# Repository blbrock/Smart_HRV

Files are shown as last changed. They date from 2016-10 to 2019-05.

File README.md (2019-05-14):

# Smart HRV  
Smart HRV replaces OEM controllers for Carrier (and probably Venmar and other brand) Heat Recovery Ventilation  
units.  Smart HRV adds intelligence to system controls using indoor and outdoor sensors to montior humidity and  
to manage humidity, fresh air, and odor control optimal performance. Smart HRV also integrates with fan and dehumidifier  
controls on Nest thermostats.  The system consists of an arduino-based control unit, one or more indoor humidity sensors.  
An outdoor temperature and humidity sensor, and an android user interface app to provide monitoring and control of system   
functions.  
  
The current system is customized to our own application and will likely need modification for other applications. But the   
package includes basic serial control logic for controlling an HRV and hopefully can provide guidance for others wishing  
to improve permormance of their heat recovery ventialation systems.  
  
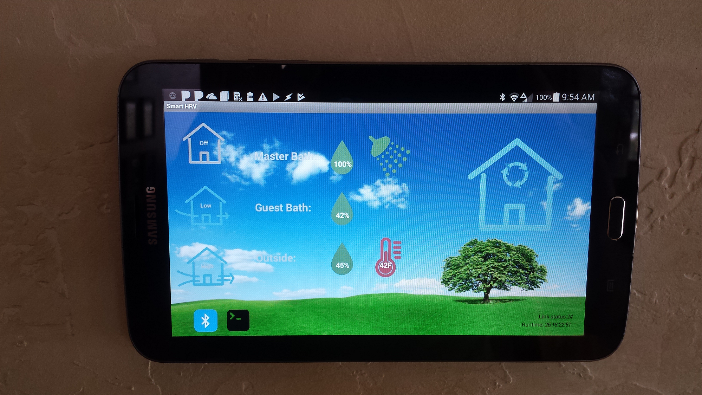
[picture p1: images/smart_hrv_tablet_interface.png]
Smart HRV Control Panel
  
  
# Background  
HRV and ERV (Energy Recovery Ventillator) have three basic functions:  
  
1. Manage indoor air quality efficiently by exchange fresh outdoor air for stale indoor air while recovering a portion of the heat from the exhaust airstream to conserve energy. 
 
2. Manage indoor humidity to reduce damage around windows and other cold surfaces by exchanging moist indoor air with dryer outdoor air; again recovering a portion of the heat from the exhaust air stream.  

3. Manage odors by exhausting indoor air.  
  
HRV/ERV systems work very well but the controls that came with ours (and most other units) fail on all three of their intended tasks.  Many units like ours lack any sort of timer circuit to allow fresh air exchange to be cycled. Instead, manufacturers and many HVAC expert claim the unit should be run continuously to maintain a steady flow of fresh air. This is insane! Heat recovery efficiency ranges from around 60%-70% for HRV units like ours, to about 90% for the newest ERV units. That means for every cubic foot of air exhausted by our unit, we lose 40% of the heat it contains. Heat we paid dearly to produce! Sure, it's better than opening a window but cycling the unit can provide plenty of fresh air while saving a significant amount of heat. Second, the best humidity to keep your house in winter depends on the outside temperature. The colder it is outside, the more likely moisture is to condense on windows so you need lower indoor humidity to prevent it. Also, the ability to reduce humidity by echanging indoor and outdoor air depends on the humidity outside. Luckily, outdoor humidity drops with the temperatue so on cold days, there is a good chance it is dryer outside than inside. But still, basic HRV units have no way to know if exchanging air will help and they could run in futility without reducing indoor humidity on wet days. Basic controllers have a manual dial setting to adjust the target indoor humidity. But outdoor temperatures fluctuate wildly over the day and season and nobody has the time to constantly fiddle with the dial to guess what the weather is going to do. This leads to settings that either run too little or too much so wind up with condensation damage on the windows anyway, wasted heat loss, or both. Finally, HRV/ERV units often include manual push buttons installed in bathrooms and laundry rooms that run for a set time when humidity or odor control is needed. OUrs ran for 20 minutes on a push which was not enough time to eliminate humidity after a shower, and certainly not enough time to eliminate odors when the relatives are visiting.

After years of frustration and some band-aid fixes for these inadequate controls, the catalyst to do something came when I purchased several Nest thermostats for our house and realized they provided fan and dehumidifier control functions that could improve the situation.  The fan control provided adjustable fresh air cycling and the dehumidifier provided the possibility of continuously monitoring outdoor temps and updating the humidity setpoint to always have the HRV trying to achieve the optimal humidity. I thought it would be just a matter of throwing in a couple of relays to get the Nest talking to the HRV but I was wrong.  There is no provision for such a setup so the only good option was to hack the controller.  So I set about reverse engineering the serial ttl communication logic, tossing out the old ugly wall controller and replacing it with an arduino controller interfaced with a cheap used android tablet mounted on the wall. The result is the Smart HRV system which has been chugging along with continuous tweaks for about two years now.

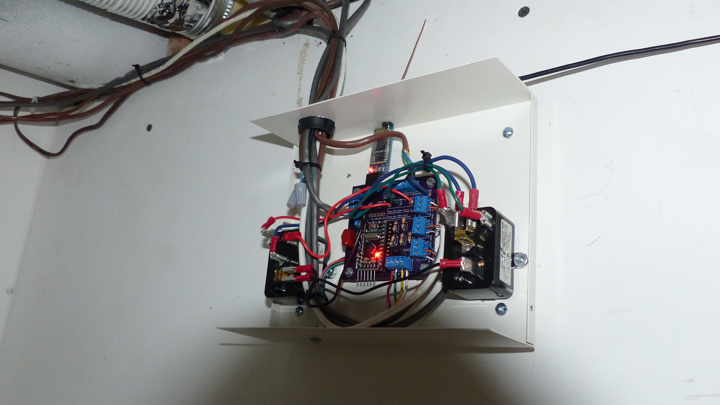
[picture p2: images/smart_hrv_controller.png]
Smart HRV Controller
  
  
# Features: 

1. Monitors indoor humidity in multiple rooms and outdoor temperature and humidity to automatically and intelligently determine optimal inddor humidity levels and initiate fresh air exchange or recirculation cycles to achieve target humidity with minimal heat loss.

2. Integrates with Nest thermostat to allow fan controls on thermostat to initiate low speed air exchange cycles.

3. Defrost indicator on user interface to show when a defrost recirculating cycle is active.

4. Tracks cumulative run time and alerts users when it is time to service filters.  

# Extras:  

# Error checking and logging:   

# Known Bugs:

- The HRV unit may enter an error condition if someone manually presses a ventilation button in a bathroom while an automated dehumidification cycle is already in progress.  This appears to be due to some internal control logic within the HRV.  My work around is to power cycle the HRV unit if that happens to reset the error condition.  A better solution would be to wire the manual ventilation buttons directly to the arduino control panel and modify the control panel schematic and arduino sketch to bypass the internal HRV controller for handling manual ventilation requests.

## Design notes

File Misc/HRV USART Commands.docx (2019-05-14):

System Startup

Receive 28(0x1C)

Send ‘188(0x8C)

Send 236(0xEC)

Receive 28(0x1C)

Send ‘188(0x8C)

Send 236(0xEC)

Receive 220(0xDC)

Send ‘188(0x8C)

Send 236(0xEC)

Receive 188(0xBC)

Send 236(0xEC)

Receive 220(0xDC)

Send ‘188(0x8C)

Receive 188(0xBC)

Low Speed Exchange

Send 140(0x8C)

Receive 188(0xBC)

Wait to receive 92(0x5C)

Send ‘188(0x8C)

High Speed Exchange

Send 76(0x4C)

Receive ‘188’(0xBC)

Wait to receive 92(0x5C)

Send ‘188’(0x8C)

Timer

Receive 92(0x5C)

Send ‘188’(0x8C)

End Timer

Tx 255

Rx 220

Tx 188

Cancel Timer

Wait to receive ‘220’(0xDC)

Send ‘188’(0x8C)

Off

Send ‘236’(0xEC)

Receive ‘188’(0xBC)

Receive ‘220’(0xDC)

Send ‘188’(0xBC)

Auto

Send ‘12’(0x0C)

Receive ‘188’(0xBC)

Receive ‘220’(0xDC)

Send ‘188’(0x8C)

Recirculate

Send ‘172’(0xAC)

Receive ‘188’(0xBC)

Receive ‘220’(0xDC)

Send ‘188’(0x8C)

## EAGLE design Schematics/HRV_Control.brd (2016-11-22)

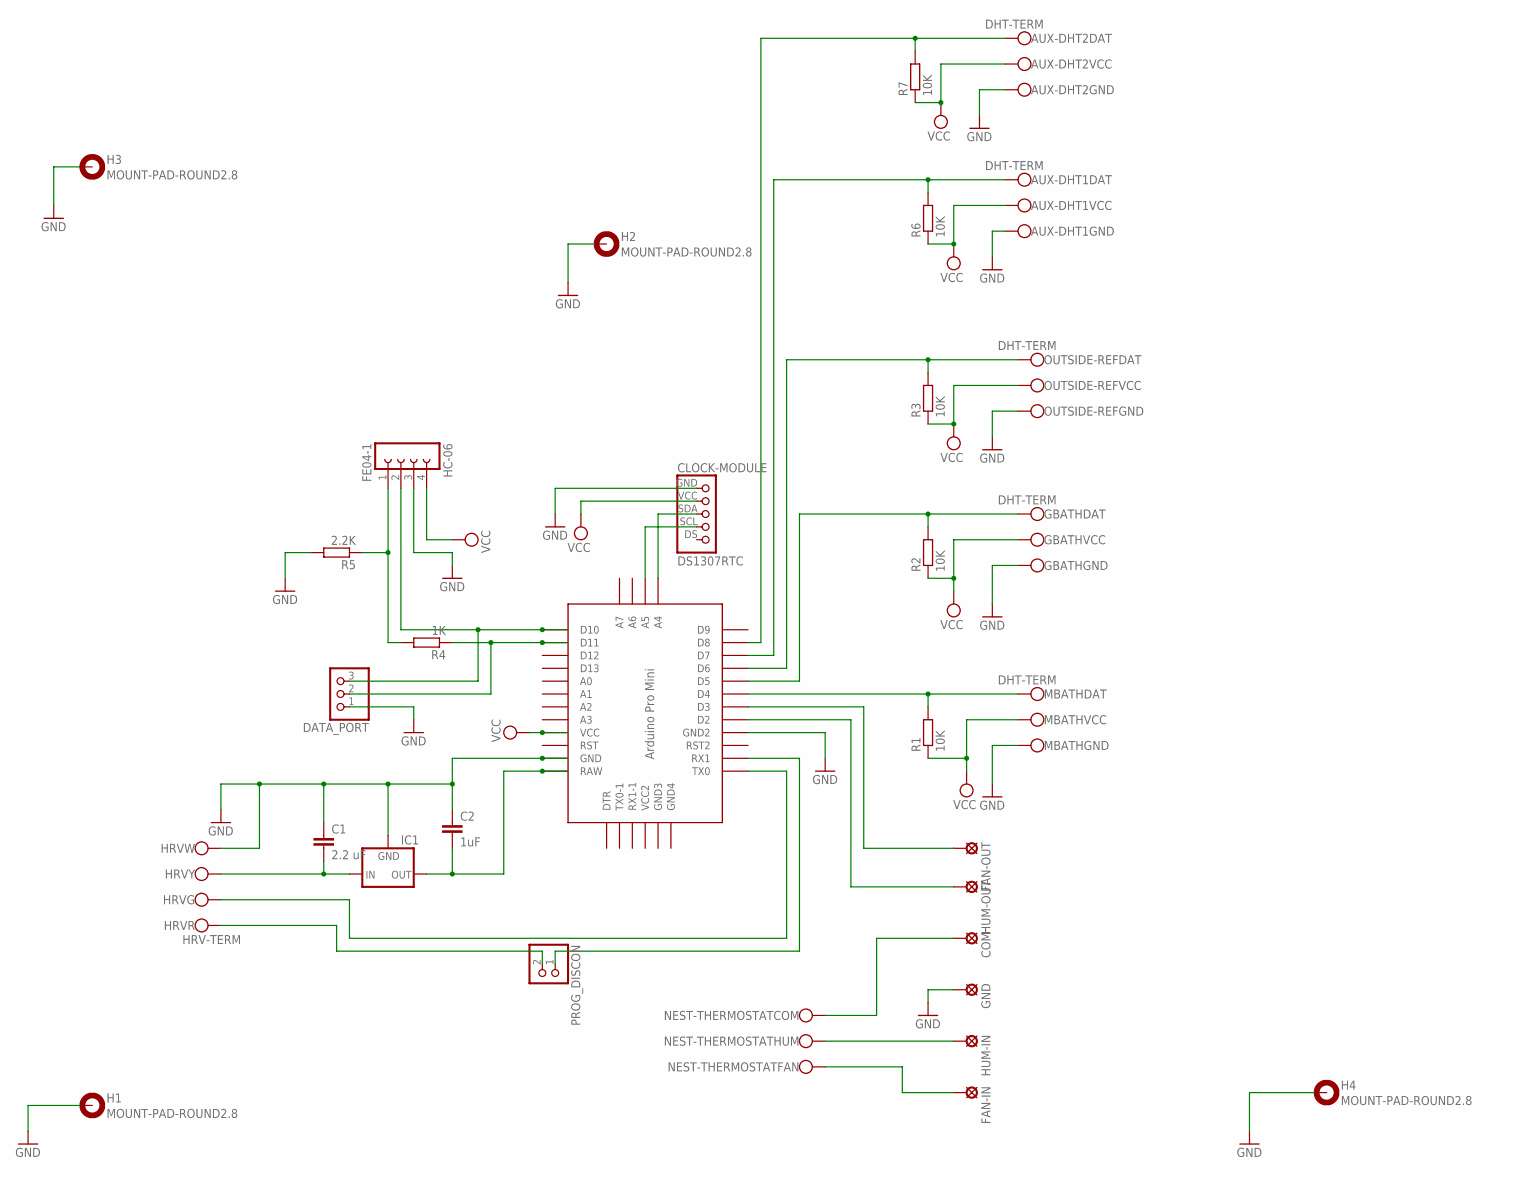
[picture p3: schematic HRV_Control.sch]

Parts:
AUX-DHT1, AUX-DHT2: DHT-TERM; DHT-TERMINAL
C1: 2.2 uF; C5B3
C2: 1uF; C025-024X044
CLOCK-MODULE: DS1307RTC
COM: SE14
DATA_PORT: PINHD-1X3; 1X03
FAN-IN: SE14
FAN-OUT: SE14
GBATH: DHT-TERM; DHT-TERMINAL
GND: SE14
H1, H2, H3, H4: MOUNT-PAD-ROUND2.8; 2,8-PAD
HC-06: FE04-1
HRV: HRV-TERM
HUM-IN: SE14
HUM-OUT: SE14
IC1: 78XXL
MBATH: DHT-TERM; DHT-TERMINAL
NEST-THERMOSTAT: NEST-TERM
OUTSIDE-REF: DHT-TERM; DHT-TERMINAL
PROG_DISCON: PINHD-1X2; 1X02
R1, R2, R3, R6, R7: 10K; 0204/7
R4: 1K; 0204/7
R5: 2.2K; 0204/7
U$6: PRO-MINI

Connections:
GND: AUX-DHT1.GND, AUX-DHT2.GND, C1.1, C2.1, CLOCK-MODULE.GND, DATA_PORT.1, GBATH.GND, GND.MP, H1.B2,8, H2.B2,8, H3.B2,8, H4.B2,8, HC-06.3, HRV.W, IC1.GND, MBATH.GND, OUTSIDE-REF.GND, R5.2, U$6.GND, U$6.GND1 (GND2)
unnamed: C1.2, HRV.Y, IC1.IN
unnamed: FAN-IN.MP, NEST-THERMOSTAT.FAN
unnamed: C2.2, IC1.OUT, U$6.RAW
unnamed: HRV.G, U$6.TX0
unnamed: PROG_DISCON.1, U$6.RX1
unnamed: MBATH.DAT, R1.2, U$6.D4
unnamed: HC-06.1, R4.2, R5.1
unnamed: HUM-IN.MP, NEST-THERMOSTAT.HUM
unnamed: COM.MP, NEST-THERMOSTAT.COM
unnamed: OUTSIDE-REF.DAT, R3.2, U$6.D6
unnamed: GBATH.DAT, R2.2, U$6.D5
unnamed: FAN-OUT.MP, U$6.D3
unnamed: HUM-OUT.MP, U$6.D2
unnamed: HRV.R, PROG_DISCON.2
unnamed: AUX-DHT1.DAT, R6.2, U$6.D7
unnamed: AUX-DHT2.DAT, R7.2, U$6.D8
SCL: CLOCK-MODULE.SCL, U$6.A5
SDA: CLOCK-MODULE.SDA, U$6.A4
SRX: DATA_PORT.2, R4.1, U$6.D11
STX: DATA_PORT.3, HC-06.2, U$6.D10
VCC: AUX-DHT1.VCC, AUX-DHT2.VCC, CLOCK-MODULE.VCC, GBATH.VCC, HC-06.4, MBATH.VCC, OUTSIDE-REF.VCC, R1.1, R2.1, R3.1, R6.1, R7.1, U$6.VCC

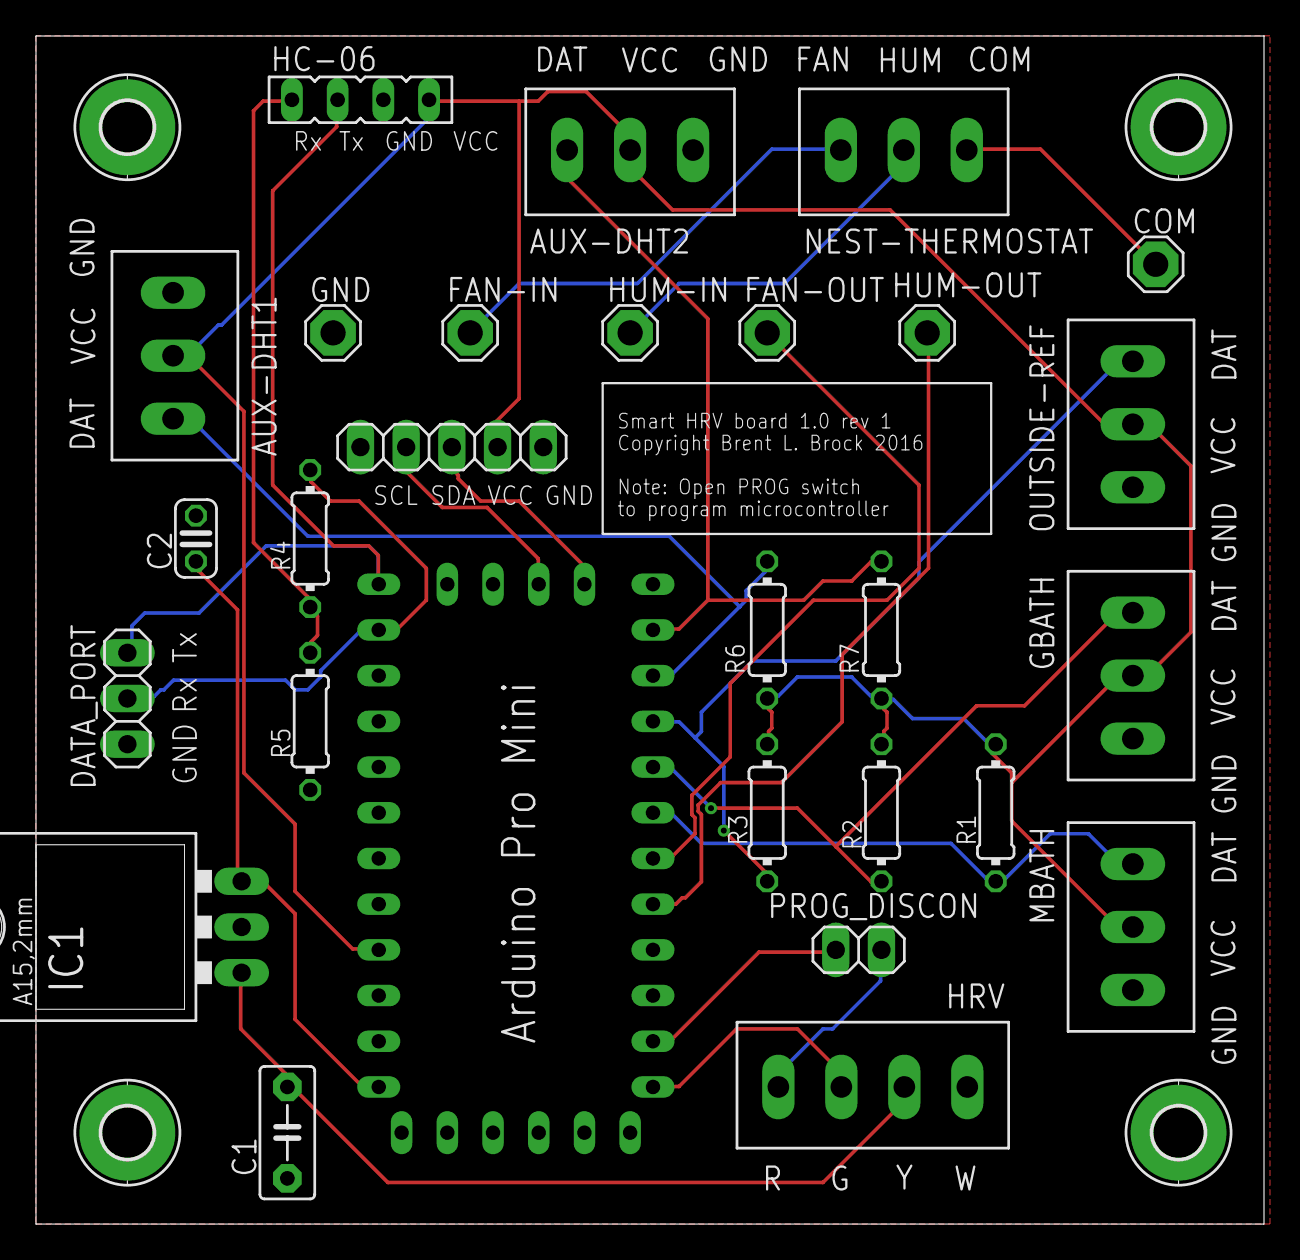
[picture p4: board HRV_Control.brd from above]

Board: 2 copper layers, 68.2 x 66.0 mm, 32 parts (0 on the bottom side), 22 nets.

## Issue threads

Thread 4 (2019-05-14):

HRV enters error condition if manual vent button pressed during automatic dehumidify cycle.

blbrock, 2019-05-14:
The HRV unit may enter an error condition if someone manually presses a ventilation button in a bathroom while an automated dehumidification cycle is already in progress.  This appears to be due to some internal control logic within the HRV.  My work around is to power cycle the HRV unit if that happens to reset the error condition.  A better solution would be to wire the manual ventilation buttons directly to the arduino control panel and modify the control panel schematic and arduino sketch to bypass the internal HRV controller for handling manual ventilation requests.

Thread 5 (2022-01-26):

ERV Controller in isolation

trevorbroad, 2022-01-26:

blbrock, 2022-01-28:
Hi Trevor,

Thanks for you interest in this little project.  I’m swamped with work right now but will get back to you soon with answers to your questions.

Brent

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

trevorbroad, 2022-02-01:
Thanks for your response! I've since figured out the above questions for the most part. The jumper disconnect is for when connecting a programmer, and I've ignored the capacitors and instead am running Y through a buck converter to the 5v pin.

What I'm trying to figure out now is what codes activate which functions on my ERV. How did you figure this out? Especially the request/response/request patterns? (ie. send 140, wait for 92, send 188) - what do the request and response codes translate to? The codes in your script don't seem to work for me. I hacked apart the script as well, as I really only need functions to turn on/off and low/high for the ERV. All other logic will be inside my Home Assistant installation.

Also, maybe you can validate my upload and test process - I pull the R jumper to send the updated firmware to the controller, then reconnect R, but I leave the programmer connected, so I can monitor the serial output. Is this ok or are there risks of conflicts with having both the programmer attached and R connected at the same time? (I'm still new to arduino and programming for hardware)

Closed 2022-01-28.

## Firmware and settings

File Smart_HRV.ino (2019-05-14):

\
#include <RunningAverage.h>
#include <SoftwareSerial.h>
// #include <avr/wdt.h>;
/*
  Switched to DHT library developed by Rob Tillaart
  (https://github.com/RobTillaart/Arduino/tree/master/libraries/DHTlib)
  This library reads both temperature and humidity from
  a sensor with a single poll.  This solved a problem with the outdoor reference
  sensor hanging after several hours of use. This hanging appears to be caused by
  timing issues with float polling to extract both temp and humidity readings from
  that sensor.
*/
#include <dht.h>
//#include <EEPROM.h>

dht DHT;

// Define input pins
const int dehumPin = 2; // Dehumidification relay pin
const int fanPin = 3; // Fresh air fan relay pin
const int mBathPIN = 4;  // Master bath pin
const int gBathPIN = 5;  // Guest bath pin
const int refPIN = 6;  // Outside reference pin
const int mediaRmPIN = 7; // Indoor reference in media room

byte cmd = 4;
byte last_cmd;
int RxByte;
bool autoState = true;
bool recircState = true;
bool fanOn = false;
bool dehumCall = false;
bool defrost = false;
int minTempThresh = 5;
float rft;
int debug = 0;
String dataList = "";
int samples = 0;
unsigned long startTime = 0;
unsigned long dhStartTime = 0;

RunningAverage mbhRA(5);
RunningAverage gbhRA(5);
RunningAverage mrhRA(5);
RunningAverage mbtRA(5);
RunningAverage gbtRA(5);
RunningAverage mrtRA(5);
RunningAverage rfhRA(5);
RunningAverage rftRA(5);

SoftwareSerial TxSerial(10, 11); // RX, TX

void setup() {
  Serial.begin(300);
  TxSerial.begin(9600);
  //  TxSerial.println("Serial communication initialized");

  pinMode(13, OUTPUT);
  digitalWrite(13, LOW);    // turn the LED off by making the voltage LOW to save a little energy
  pinMode(dehumPin, INPUT_PULLUP);
  pinMode(fanPin, INPUT_PULLUP);

  // explicitly start clean
  mbhRA.clear();
  gbhRA.clear();
  mrhRA.clear();
  mbtRA.clear();
  gbtRA.clear();
  mrtRA.clear();
  rfhRA.clear();
  rftRA.clear();

  int dhp = HIGH;
  int chk = DHT.read21(refPIN);
  if (chk == 0 ) {
    //rftCelsius = DHT.temperature;
    // Convert rft to Fahrenheit
    rft = round (rft * 1.8 + 32);
  }

  // Initialize startup handshake
  startup();
  cmd = 236; //Reset cmd and last_cmd after startup
  last_cmd = 236;
  // wdt_enable(WDTO_8S);
}

void loop() {
  //dataList = "";
  if (recircState) defrost = false;
  // wdt_reset();
  // Get commands from HRV
  RxByte = read_Tx(); // Read any incoming signals from HRV unit

  // Check relay pins for status of thermostat calls
  if (autoState) {
    CheckRelays(rft);
    //    SetRelays();
  }

  // Humidity sensors take precedent over relays or HRV/Timer commands
  rft = CheckHumidity();

  /* Get commands from TxSerial monitor and send as digital byte
    to HRV. Note that placement of TxSerial read here allows manual commands to
    override any programatic commands set earlier in the loop */
  ManCmd();

  // Execute Commands
  ExecCmds();

  delay(2000);
  if (debug >= 3) {
    Debug();
    delay(2000);
  }
  // Send data to android via bluetooth
  if (debug == 0) {
    dataList = dataList + String(last_cmd) + ',' + String(defrost) + ',';
    TxSerial.println(dataList);
    dataList = "";
  }
  Serial.flush(); // flush any bytes remainining in sending buffer

  // If manual mode lasts > 4 hours, return to automatic mode
  if (!autoState) {
    if (millis() - startTime > 14400000) {
      cmd = 236;
      autoState = true;
      startTime = 0;
    }
  }
}

//////////////////////////////////////////////////////////////////////////////////////////////////////////////////
///////////////////////////////////////////// FUNCTIONS //////////////////////////////////////////////////////////
//////////////////////////////////////////////////////////////////////////////////////////////////////////////////

// Read Serial communications
byte read_Tx() {
  delay(100); // Wait to allow time to receive signal time delay value seems critical
  if (Serial.available() > 0) {
    RxByte = Serial.read();
    if (debug >= 1) {
      TxSerial.print("Rx: ");
      TxSerial.println(RxByte, DEC);
    }
  }
  return RxByte;
}

// Write Serial communications
void write_Tx(byte cmd) {
  Serial.write(cmd);
  if (debug >= 1) {
    TxSerial.print("Tx: ");
    TxSerial.println(cmd);
  }
}

////////////////////////////////// Run initial handshake on system startup //////////////////////////////////////
void startup() {
  //Startup Handshake
  for (int times = 0; times < 3; times++) {
    delay(200);
    //    TxSerial.println("Startup waiting for 28...");
    RxByte = read_Tx();
    if (RxByte == 28) {
      break;
    }
  }
  if (RxByte == 28) {
    write_Tx(188);
    delay(50);
    write_Tx(236);
    for (int i = 0; i < 3; i++) {
      for (int times = 0; times < 10; times++) {
        if (RxByte == 28 or RxByte == 220) {
          write_Tx(188);
          delay(100);
          write_Tx(236);
          break;
        }
      }
    }

    for (int times = 0; times < 10; times++) {
      if (RxByte == 188) {
        write_Tx(236);
        break;
      }
    }

    for (int times = 0; times < 10; times++) {
      RxByte = read_Tx();
      if (RxByte == 220) {
        write_Tx(188);
        break;
      }
    }
  }
  else {
    // If signal 28 not receive, use brute force initialization
    write_Tx(252);
    for (int times = 0; times < 10; times++) {
      RxByte = read_Tx();
      if (RxByte != 28) {
        //        TxSerial.println("Waiting for 28...");
        RxByte = read_Tx();
        delay(200);
      }
      else if (RxByte == 28) {
        write_Tx(188);
        break;
      }
    }
    for (int times = 0; times < 10; times++) {
      RxByte = read_Tx();
      if (RxByte != 220) {
        //        TxSerial.println("Waiting for 220...");
        RxByte = read_Tx();
        delay(200);
      }
      else if (RxByte == 220) {
        write_Tx(188);
        break;
      }
    }
  }

  TxSerial.println("Startup Complete");
  while (Serial.available()) {
    Serial.read();
    if (RxByte == 220) {
      write_Tx(188);
    }
  }
  Serial.flush();
  RxByte = 0;
  delay(30000);
}

///////////////////////////////// Check Humidity Sensors ///////////////////////////////////////////////
/*Checks multiple sensors for humidity and runs HRV to achieve optimal humidity. This routine automatically
   reduces humidity in bathrooms and other high humidity areas where sensors are installed. It also adjusts
   whole house humidity based on outside temperature to reduce condensation on windows during cold weather.
   Recirculation takes precedent to minimize heat loss and occurs whenever minimum indoor humidity < desired
   setpoint. If outside humidity is lower than desired setpoint and maximum indoor humidity is <= minimum indoor
   humidity plus 5%, then fresh air is exchanges until the maximum of desired setpoint or lowest humidity possible
   is reached. Fresh air will also be exchanged during a dehumidification cycle if thermostat is calling for
   exchange, outside temp is above the minimum threshold, and outdoor humidity is low enough to allow dehumidification
   to proceed.
*/
float CheckHumidity(void) {

  float mbh;
  float gbh;
  float mrh;
  int dhp;
  float mbt;
  float gbt;
  float mrt;
  float rftCelsius;
  float rfh;
  float humTarget;
  float humOn; // = setpointOn;
  float humOff; // = setpointOff;
  int recirc;

  // wdt_reset();
  // Get data from sensors. Use running averages
  int chk = DHT.read22(mBathPIN);
  if (chk == 0 ) {
    mbhRA.addValue(DHT.humidity);
    mbh = mbhRA.getAverage();
    mbtRA.addValue(DHT.temperature);
    mbt = mbtRA.getAverage();
  }
  chk = DHT.read22(gBathPIN);
  if (chk == 0) {
    gbhRA.addValue(DHT.humidity);
    gbh = gbhRA.getAverage();
    gbtRA.addValue(DHT.temperature);
    gbt = gbtRA.getAverage();
  }
  // wdt_reset();
  chk = DHT.read22(mediaRmPIN);
  if (chk == 0) {
    mrhRA.addValue(DHT.humidity);
    mrh = mrhRA.getAverage();
    mrtRA.addValue(DHT.temperature);
    mrt = mrtRA.getAverage();
  }
  chk = DHT.read21(refPIN);
  if (chk == 0 ) {
    rfhRA.addValue(DHT.humidity);
    rfh = rfhRA.getAverage();
    rftRA.addValue(DHT.temperature);
    rftCelsius = rftRA.getAverage();
    //rftCelsius = DHT.temperature;
    // Convert rft to Fahrenheit
    rft = round(rftCelsius * 1.8 + 32);
  }

  // wdt_reset();
  samples++;
  if (samples == 100)
  {
    samples = 0;
    mbhRA.clear();
    gbhRA.clear();
    mrhRA.clear();
    mbtRA.clear();
    gbtRA.clear();
    mrtRA.clear();
    rfhRA.clear();
    rftRA.clear();
  }

  /* Convert indoor and outdoor relative humidity to absolute humidity to allow comparison of
      water holding capacity for setting humidity on/off setpoints.
  */
  float tempIndoor = (mbt + gbt + mrt) / 3;
  float hMax = max(mbh, max(gbh, mrh)); // highest indoor sensor
  float hMin = min(mbh, min(gbh, mrh));
  float hAvg = ((mbh + gbh + mrh) - hMax) / 2; // = average of 2 lowest indoor sensors
  float h;
  // Use maximum humidity only when humidity is raised in bathrooms (e.g. shower), otherwise use average
  if (hMax - hMin > 10) h = hMax;
  else  h = hAvg;
  h = calcAbsH(tempIndoor, h);
  float Absh = calcAbsH(tempIndoor, h);
  float AbsHumIndoor = calcAbsH(tempIndoor, hAvg);
  float AbsHumOutdoor = calcAbsH(rftCelsius, rfh);
  float minRecirc = AbsHumIndoor * 1.2;

  /*
        Calculate minimum humidity that can be achieved - indoor humidity calculated as the average
        humidity of the two lowest reading sensors. Minimum achievable recirculating humidity is
        absolute indoor humidity times 1.2. Minimum humidity achievable is minimum of minRecirc and absolute
        outdoor humidity time 2.1. Multipliers are arbitrary values designed to avoid setting humidity off setpoints
        that are unrealistically low, which results in continuous running of HRV without affecting humidity.
  */
  float minHum = min(AbsHumOutdoor * 2.1, minRecirc);
  //float minHum = min(rfhAdj + 2, minRecirc);

  if (debug == 0) {
    dataList = String(rft) + ',' + String(int(round(rfh))) + ',' + String(int(round(mbh))) + ',' + String(int(round(gbh))) + ',';
  }

  // Set target humidity based on outside temperature

    humTarget = float(((0.56 * rft) + 32) - 2.5);
 // humTarget = float(((0.4603 * rft) + 32) - 2.5);

  // Set max humidity to 60% if possible
  if (humTarget > 60 and minHum < 60) humTarget = 60;
  // set min humidity to avoid running fresh air exchange during extreme cold
  else if (humTarget < 26) humTarget = 26;

  float AbsHumTarget = calcAbsH(tempIndoor, humTarget);

  /* if minimum achievable humidity is > humTarget, adjust humidity setpoints
    to minimum humidity possible */
  if (AbsHumTarget < minHum) {
    humOff = minHum;
  }

  // Shut off HRV when humidity drops to target or minimum achievable humidity
  else {
    humOff = AbsHumTarget;
  }

  /* If it's really cold outside, adjust humOff upward slightly to prevent continuous
    run without achieving humidity shutoff.
  */
  if (rft < minTempThresh) humOff = humOff * 1.25;

  humOn = humOff + 1;


  // Check dehumidity relay to see if Nest is calling for dehumidification
  dhp = digitalRead(dehumPin);
  if (dhp == LOW) {
    digitalWrite(13, HIGH);
  }
  // Set dehumidication call on/off. Start/check timer to run dh call minimum of 15 minutes to prevent short cycling.
  if (h >= humOn or (dhp == LOW and h > minHum)) {
    dehumCall = true;
    if (dhStartTime == 0) dhStartTime = millis();
  }
  else if (millis() - dhStartTime > 900000 and (h <= humOff and (dhp == HIGH) or (dhp == LOW and minHum > h + 0.5))) {
    dehumCall = false;
    recircState = true;
    dhStartTime = 0;
  }

  // Set HRV to recirculate if possible to conserve heat
  if ((h <= minRecirc) or (calcAbsH(tempIndoor, hAvg) > humOff) or (fanOn and rft > minTempThresh) or (AbsHumOutdoor <= humOff and rft >= 50)) {
    recircState = false;
  }
  else if (h > minRecirc + 1) { // or rft < minTempThresh) {
    recircState = true;
  }

  if (autoState) {
    //    Start dehumidification if humidity is > than target setpoint or Nest is calling for dehumidify
    if (dehumCall) {

      if (recircState) cmd = 172;
      else cmd = 76;
    }
    else {
      if (fanOn and rft > minTempThresh) cmd = 140;
      else cmd = 236;
    }
  }
  if (debug >= 2) {
    TxSerial.print("Outside TEMP: ");
    TxSerial.println(rft);
    TxSerial.print("Outside RH: ");
    TxSerial.println(rfh);
    TxSerial.print("Inside Ref RH: ");
    TxSerial.println(mrh);
    TxSerial.print("Master Bath RH: ");
    TxSerial.println(mbh);
    TxSerial.print("Guest Bath RH: ");
    TxSerial.println(gbh);
    TxSerial.print("humTarget: ");
    TxSerial.println(humTarget);


    if (debug >= 3) {
      TxSerial.println();
      TxSerial.print("h: ");
      TxSerial.println(h);
      TxSerial.print("humOn: ");
      TxSerial.println(humOn);
      TxSerial.print("humOff: ");
      TxSerial.println(humOff);
      TxSerial.print("minRecirc: ");
      TxSerial.println(calcRelH(tempIndoor, minRecirc));
      TxSerial.print("AbsHumOutdoor: ");
      TxSerial.println(AbsHumOutdoor);
      TxSerial.print("AbsHumTarget: ");
      TxSerial.println(AbsHumTarget);

      if (debug >= 4) {
        TxSerial.println();
        TxSerial.println();
        TxSerial.print("Dehum Relay: ");
        TxSerial.println(dhp);
      }
    }

  }
  return rft;
}

///////////////////////////////// Check Relay Pins for Input Commands ////////////////////////////

void CheckRelays(float rft) {
  int fp = digitalRead(fanPin);
  int dhp = digitalRead(dehumPin);

  // Don't initiate fresh air exchange if outside temp is too cold
  // CheckHumidity() will handle fresh air call if dehumidification in progress
  if (fp == LOW) {
    fanOn = true;
    if (rft > minTempThresh and !dehumCall) {
      cmd = 140;
      digitalWrite(13, HIGH);
    }
  }
  else if (fanOn and fp == HIGH) {
    digitalWrite(13, LOW);
    fanOn = false;
    if (!dehumCall) {
      cmd = 236;
    }
  }
  if (fp == HIGH and dhp == HIGH) digitalWrite(13, LOW);
}

/////////////////////////// Execute Commands ///////////////////////////
void ExecCmds() {
  if (debug >= 1) {
  }
  // Don't send command if it is is zero or a repeat of last command sent
  if ((cmd != 255 and cmd != last_cmd) or (RxByte == 92 or RxByte == 220 or RxByte == 236)) {
    // if (cmd == 255) cmd = 236;
    ///// Execute HRV Requests /////
    if (cmd > 5 ) {
      write_Tx(cmd);
    }
    // 20-Minute Timer
    if (RxByte == 92) {
      /* send Ak if defrost signal (92) received. I've found no way
          to tell the difference between 92 sent from pressing a wall switch
          and one sent to signal defrost. The partial solution is to assume
          that 92 sent during dehumidification is a defrost call. A defrost call
          low speed fresh air exchange could be misinterpreted as a wall switch
          push and initiate high speed exchange timer.

      */
      if (dehumCall or last_cmd == 76 or last_cmd == 140) {
        Ak();
        if (defrost) {
          defrost = false;
          if (cmd = 76) last_cmd = 76;
        }
        else {
          defrost = true;
          last_cmd = 172;
        }
      }
      else  Timer();
      last_cmd = cmd;
    }
    // Acknowledge Keep Alive Request
    else if (RxByte > 0 and RxByte < 255) {
      // else if (RxByte == 220 or RxByte == 28 or RxByte == 92) {
      Ak();
    }
    // Auto, Off, Recirculate Modes
    else if (cmd == 12 or cmd == 172 or cmd == 236) {
      last_cmd = cmd;
      defrost = 0;

      AutoOffRecirc();
    }
    // High, Low Fresh Air Exchange Modes
    else if (cmd == 76 or cmd == 140) {
      last_cmd = cmd;
      Xchange();
    }
    else {
      TxSerial.println("Man Cmd");
      write_Tx(cmd);
    }
  }

  while (TxSerial.read() >= 0); // flush the receive buffer
  while (Serial.read() >= 0); // flush the receive buffer
}

/////////////////////////////////////// Manual Command Mode ///////////////////////////////////////
/* Get commands from TxSerial monitor and send as digital byte
  to HRV. Note that placement of TxSerial read here allows manual commands to
  override any programatic commands set earlier in the loop */

void ManCmd() {
  if (TxSerial.available()) {
    byte tx = TxSerial.parseInt();
    // Set Debug level if it has changed
    if (tx != debug and tx <= 4) {
      debug = tx;
      TxSerial.print("Debug Level - ");
      TxSerial.println(debug);
    }
    else if (tx > 5 and tx < 255) {
      cmd = tx; // Send manual command
      // Enter manual command mode
      if (autoState) {
        if (cmd == 236 and last_cmd == 236) ; // Don't toggle autoState on repeat off command
        else  {
          autoState = false;
          startTime = millis();
        }
      }
      else if (cmd == 236) autoState = true;
    }

    // Sometimes 0 values get stuck in buffer for some reason. This clears them out.
    while (TxSerial.available()) {
      TxSerial.read();
    }
  }
}

/////////////////// Auto, Off and Recirculate Modes ////////////////////
void AutoOffRecirc(void) {
  // wdt_reset();
  // Wait for acknowledgement that command was received. If not, repeat command up to 3 times
  for (int times = 0; times < 3; times++) {
    delay(200);
    RxByte = read_Tx();
    if (RxByte != 188 and RxByte != 92) {
      write_Tx(cmd);
    }
    else {
      break;
    }
  }
  // wdt_reset();
  for (int times = 0; times < 6; times++) {
    RxByte = read_Tx();
    if (RxByte != 220) {
      RxByte = read_Tx();
      delay(700);
    }
    else if (RxByte == 220) {
      write_Tx(188);
      while (RxByte = Serial.read() >= 0); // flush the receive buffer to avoid unwanted commands sent
      break;
    }
  }
  Serial.flush();
}

/////////////////////////////////// Fresh Aire Exchange Modes /////////////////////////////////////
void Xchange(void) {
  // Wait for acknowledgement that command was received. If not, repeat command up to 3 times
  for (int times = 0; times < 3; times++) {
    delay(200);
    RxByte = read_Tx();
    if (RxByte != 188 and RxByte != 92) {
      write_Tx(cmd);
    }
    else if (RxByte == 188) {
      break;
    }
  }
  for (int times = 0; times < 10; times++) {
    RxByte = read_Tx();
    if (RxByte != 92) {
      RxByte = read_Tx();
      delay(700);
    }
    else if (RxByte == 92) {
      write_Tx(188);
      while (RxByte = Serial.read() >= 0); // flush the receive buffer to avoid unwanted commands sent
      RxByte = 0;
      break;
    }
    else {
      RxByte = 0;
    }
  }
}

////////////////////////////////// 30-Minute Timer Function /////////////////////////////////
void Timer(void) {
  autoState = false;
  startTime = millis();
  byte Tx;
  int times = 0;
  // wdt_reset();
  write_Tx(188);
  //  if (debug >= 1) {
  //    TxSerial.println("Starting 30 min timer");
  //  }
  //30 min = 1800000 ms
  //20 min = 1200000 ms
  while (millis() - startTime < 1200000) {
    // Report data via bluetooth while timer running

    CheckHumidity();
    dataList = dataList + String(92) + ',' + String(defrost) + ',';
    TxSerial.println(dataList);
    dataList = ""; // clear old data list

    RxByte = read_Tx();
    if (TxSerial.available()) {
      Tx = TxSerial.parseInt();
    }
    if (Tx != debug and Tx <= 4) {
      debug = Tx;
      TxSerial.print("Debug Level - ");
      TxSerial.println(debug);
    }
    else if (Tx == 220 || Tx == 236 || Tx == 255 || RxByte == 220 || RxByte == 255 || (times > 0 && RxByte == 92)) { // if wall switched pushed again, cancel timer
      //      if (debug >= 1) {
      //        TxSerial.println("Timer Cancel Request Recieved");
      //      }
      break;
    }
    else if (RxByte > 0) {
      write_Tx(188);
    }
    RxByte = 0;
    delay(2000);
  }

  //  if (debug >= 1) {
  //    TxSerial.println("Timer stopped");
  //  }

  // Shut down HRV unless timer ended by button push
  if (RxByte != 220 and RxByte != 92) StopTimer();

  // Return to auto mode and report that ventilation has stopped.
  autoState = true;
  cmd = 236;
}
////////////////////// Stop Timer ////////////////////////////////
void StopTimer(void) {
  write_Tx(252); // Had to guess at this command through trial and error.
  for (int times = 0; times < 10; times++) {
    // wdt_reset();
    RxByte = read_Tx();
    if (RxByte != 28) {
      RxByte = read_Tx();
      delay(400);
    }
    else if (RxByte == 28) {
      write_Tx(188);
      break;
    }
  }
  for (int times = 0; times < 10; times++) {
    // wdt_reset();
    RxByte = read_Tx();
    if (RxByte != 220) {
      RxByte = read_Tx();
      delay(400);
    }
    else if (RxByte == 220) {
      write_Tx(188);
      break;
    }
  }
  cmd = 236;
}

///////////////////////////////// Acknowledge Keep Alive Request //////////////////////////
void Ak(void) {
  write_Tx(188);
  while (Serial.read() >= 0); // flush the receive buffer
  Serial.flush();
  RxByte = 0;
}

/////////////////////////////////// Calculate Dewpoint (fast method) ////////////////////////
//// delta max = 0.6544 wrt dewPoint()
//// 6.9 x faster than dewPoint()
//// reference: http://en.wikipedia.org/wiki/Dew_point
//float dewPointFast(float celsius, float humidity)
//{
//  float a = 17.271;
//  float b = 237.7;
//  float temp = (a * celsius) / (b + celsius) + log(humidity * 0.01);
//  // wdt_reset();
//  float Td = (b * temp) / (a - temp);
//  return Td;
//}
//
/////////////////////////////////// Calculate Humidity //////////////////////////////////////
//// reference: http://andrew.rsmas.miami.edu/bmcnoldy/Humidity.html
//
//int humidityAdj(float celsius, float dewpoint)
//{
//  // wdt_reset();
//  int humAdj = 100 * (exp((17.625 * dewpoint) / (243.04 + dewpoint)) / exp((17.625 * celsius) / (243.04 + celsius)));
//  // wdt_reset();
//  return humAdj;
//}
//
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

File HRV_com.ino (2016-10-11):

#include <SoftwareSerial.h>
#include <avr/wdt.h>;
/*
  Switched to DHT library developed by Rob Tillaart
  (https://github.com/RobTillaart/Arduino/tree/master/libraries/DHTlib)
  This library reads both temperature and humidity from
  a sensor with a single poll.  This will hopefully solve a
  problem with the outdoor reference sensor hanging after several hours of use.
  This hanging appears to be caused by timing issues with double polling to extract
  both temp and humidity readings from that sensor.
*/
#include <dht.h>
#include <EEPROM.h>

dht DHT;

#define mBathPIN 4   // Master bath pin
#define gBathPIN 5   // Guest bath pin
#define refPIN 6   // Outside reference pin

byte cmd = 4;
byte last_cmd;
int RxByte;
const int dehumPin = 2;
int dehumPinState = 0;
int dhp = 1;
const int fanPin = 3;
int fanPinState = 0;
int fp = 1;
int dhtState = 0;
float setpointOn = 60;
float setpointOff = 55;
float humOn = setpointOn;
float humOff = setpointOff;
float hMin = setpointOff; // Intitialize minimum humidity that can be obtained
int humVal = 55;
byte prehumcmd = 0;
int debug = 0;
String dataList = "";

SoftwareSerial TxSerial(10, 11); // RX, TX

void setup() {

  Serial.begin(300);
  TxSerial.begin(9600);
  TxSerial.println("Serial communication initialized");

  pinMode(13, OUTPUT);
  digitalWrite(13, LOW);    // turn the LED off by making the voltage LOW to save a little energy
  pinMode(dehumPin, INPUT_PULLUP);
  pinMode(fanPin, INPUT_PULLUP);

  // Initialize startup handshake
  startup();
  cmd = 0; //Reset cmd and last_cmd after startup
  last_cmd = 0;
  wdt_enable(WDTO_8S);
}

void loop() {
  if (debug >= 4) {
    TxSerial.print("Start Loop, cmd = ");
    TxSerial.println(cmd);
    TxSerial.print("last_cmd: ");
    TxSerial.println(last_cmd);
  }
  dataList = "";
  wdt_reset();
  // Get commands from HRV
  //  if (Serial.available() >= 0) {
  RxByte = read_Tx(); // Read any incoming signals from HRV unit

  // Check relay pins for status of thermostat calls
  if (dhtState == 0) {
    CheckRelays();
  }
  SetRelays();

  // Humidity sensors take precedent over relays or HRV/Timer commands
  CheckHumidity();

  /* Get commands from TxSerial monitor and send as digital byte
    to HRV. Note that placement of TxSerial read here allows manual commands to
    override any programatic commands set earlier in the loop */
  if (debug >= 4) {
    TxSerial.println("Listening for command");
  }
  if (TxSerial.available()) {
    byte tx = TxSerial.parseInt();
    // Set Debug level if it has changed
    if (tx != debug and tx <= 5) {
      debug = tx;
      TxSerial.print("Debug Level - ");
      TxSerial.println(debug);
    }
    else if (tx > 5) cmd = tx; // Send manual comman
    // Sometimes 0 values get stuck in buffer for some reason. This clears them out.
    if (tx == 0) {
      while (TxSerial.available()) {
        TxSerial.read();
      }
    }
  }

  // Don't send command if it is is zero or a repeat of last command sent
  if ((cmd != 0 and cmd != last_cmd) or (RxByte == 92 or RxByte == 220)) {

    if (cmd > 5) {
      write_Tx(cmd);
    }

    ///// Execute HRV Requests /////

    // Auto, Off, Recirculate Modes
    if (cmd == 12 or cmd == 172 or cmd == 236) {
      AutoOffRecirc();
    }
    // High, Low Fresh Air Exchange Modes

    else if (cmd == 76 or cmd == 140) {
      Xchange();
    }
    // 30-Minute Timer
    else if (RxByte == 92) {
      Timer();
    }
    // Acknowledge Keep Alive Request
    else if (RxByte == 220 || RxByte == 28) {
      Ak();
    }

    // Enter debug mode
    else if (cmd <= 5) {
      if (cmd != 0) debug = cmd;
      else debug = 0;
      if (cmd >= 3)Debug();
    }

    // Capture unknown commands
    else if (RxByte != 0 and RxByte != 220 and RxByte != 255 and RxByte != 92 and RxByte != 28 and RxByte != 188) {
      Capture();
    }

    else {
      TxSerial.println("Sending Manual Command");
      write_Tx(cmd);
      cmd = 0;
    }
  }

  // Repeat Command Handler
  else if (cmd != 0) {
    if (debug == 1) {
      TxSerial.println("Ignoring Repeat Command");
    }
    while (TxSerial.read() >= 0); // flush the receive buffer
    while (Serial.read() >= 0); // flush the receive buffer
    cmd = 0;
  }

  delay(2000);
  if (cmd <= 5) {
    Debug();
    delay(2000);
  }
  // Send data to android via bluetooth
  if (debug == 0) {
    dataList = dataList + String(last_cmd) + ',';
    TxSerial.println(dataList);
  }
  Serial.flush(); // flush any bytes remainining in sending buffer
}

//////////////////////////////////////////////////////////////////////////////////////////////////////////////////
///////////////////////////////////////////// FUNCTIONS //////////////////////////////////////////////////////////
//////////////////////////////////////////////////////////////////////////////////////////////////////////////////

// Read Serial communications
byte read_Tx() {
  delay(100); // Wait to allow time to receive signal time delay value seems critical
  if (Serial.available() > 0) {
    RxByte = Serial.read();
    if (debug > 0) {
      TxSerial.print("Rx: ");
      TxSerial.println(RxByte, DEC);
    }
  }
  return RxByte;
}

// Write Serial communications
void write_Tx(byte cmd) {
  Serial.write(cmd);
  if (debug > 0) {
    TxSerial.print("Tx: ");
    TxSerial.println(cmd);
  }
}
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

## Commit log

2016-10-11 Add cold weather override
    Suppresses fresh air exchange if outside temperature is < 15F.
2016-10-11 Rename sketch file
    Renamed file to be able to open it with Arduino IDE
2016-10-12 Adjust dehumidify setpoint
    Adjusted dehumidify off trigger to prevent overrun times in
    recirculation mode.
    [Smart_HRV.ino]
2016-11-02 Check Humidity update
    - added max temp parameter to prevent fresh air exchange during
    extremely cold weather
    - simplified Check_Humidity code for more efficient execution and
    readability
    - set recirculation mode as default for dehumidification to reduce heat
    loss
    [HRV_Control.brd, HRV_Control.sch]
2016-11-22 Misc. enhancements
    - Revised algorithms for fresh air and dehumidification for improved
    efficiency.
    - Added ClearEeprom function initiatated by sending code 5 from to
    microprocessor.
    - Revised circuit board to fix errors with voltage regulator pinout and
    resistor sizes.
    [HRV_Control.brd, HRV_Control.sch]
2016-11-22 Bug fix
    Fixed bug preventing HRV from going to fresh air exchange when target
    humidity < minimum indoor humidity.
    [Smart_HRV.ino]
2016-11-26 Fixed manual override
    - Changed manual command processing to prevent automation commands from
    overriding manual commands. Now manual commands sent from the control
    panel cause the processor to suspend processing of automated control
    commands until an Off (236) command is recieved, or four hours has
    elapsed since a manual command was issued.
    - Made minor adjustments to fresh air processing to improve efficiency.
    [Smart_HRV.ino]

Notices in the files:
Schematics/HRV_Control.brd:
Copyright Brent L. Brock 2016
